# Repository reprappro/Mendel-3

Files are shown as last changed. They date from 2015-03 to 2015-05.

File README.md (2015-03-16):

The RepRapPro Mendel 3 3D Printer design files repository
.
Licensed under the GPL 3, see http://www.gnu.org/copyleft/gpl.html

For more information see 

   https://reprappro.com/shop/reprap-kits/mendel-3-full-kit/

STLs of the printed parts may be found in the STL directory. A full bill of materials - itemising part numbers, descriptions and required quantities - may be found in BOM.xlsx.

Hardware components that are shared with our other printers may be found in our "Library" repository

License GPL

No guarantee is made that the files contained in this project will be free
from design faults. The user accepts the risk that some issues may arise
from printing and assembling the files contained within this project. Users
are however encouraged to publish errors/improvements back to the originator.

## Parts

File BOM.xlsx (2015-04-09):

PART NUMBER | Revision | DESCRIPTION | Category | QTY.
394 | 00-000 | DUET | ELECTRONICS | 1
545 | 00-001 | PROXIMITY SENSOR PCB | ELECTRONICS | 1
597 | 01-000 | REGULATOR PCB | ELECTRONICS | 1
111 | 00-001 | M3X8 CAP HEAD | FASTENERS | 11
112 | 00-001 | M3X25MM CAP SCREW | FASTENERS | 8
204 | 00-000 | M3 NYLOC FULL NUT | FASTENERS | 17
212 | 00-001 | M3 PLAIN WASHER | FASTENERS | 20
230 | 00-000 | M5X215MM THREADED ROD | FASTENERS | 2
241 | 00-000 | M3X20MM CAP SCREW | FASTENERS | 10
242 | 00-001 | M3X16MM CAP SCREW | FASTENERS | 7
257 | 00-000 | M3X12 CAP SCREW | FASTENERS | 16
258 | 00-000 | M3 NUT | FASTENERS | 25
465 | 00-000 | M3X50 CAP HEAD | FASTENERS | 3
520 | 00-001 | M3X35 CAP SCREW | FASTENERS | 4
543 | 00-000 | M3X30 CAP SCREW | FASTENERS | 3
581 | 00-000 | VBFS-M3-5-16 | FASTENERS | 4
689 | 00-000 | M8 NUT | FASTENERS | 78
699 | 00-000 | M8 LOCK WASHER | FASTENERS | 78
712 | 00-000 | M5 FULL NUT | FASTENERS | 2
818 | 00-000 | M3X18MM MALE/FEMALE STANDOFF VBMP-M3-5.0-18 | FASTENERS | 6
918 | 00-000 | #4 x 1/2" BUTTON HEAD SELF TAPPING SCREW | FASTENERS | 4
101 | 00-000 | CARDBOARD BOX MENDEL | HARDWARE | 1
125 | 00-000 | GLASS PRINTING PLATE | HARDWARE | 1
133 | 00-000 | CABLE TIES | HARDWARE | 1
185 | 00-000 | MICROSWITCH | HARDWARE | 1
195 | 00-000 | 5MM POLYTUBE | HARDWARE | 2
197 | 00-000 | 2.4MM BLACK HEATSHIRNK | HARDWARE | 1
199 | 00-000 | IGUS CLIP BEARING - 8MM | HARDWARE | 4
234 | 00-000 | SD CARD | HARDWARE | 1
276 | 00-000 | 15X7MM SPRING | HARDWARE | 2
279 | 00-000 | 623 BEARING | HARDWARE | 4
285 | 00-000 | PCB JUMPER | HARDWARE | 2
286 | 00-000 | KAPTON TAPE | HARDWARE | 1
287 | 00-000 | LM8UU LINEAR BEARING | HARDWARE | 6
310 | 00-000 | 608 BEARING | HARDWARE | 2
320 | 00-000 | MXL BELT - 2M | HARDWARE | 1
358 | 00-000 | 100M PLASTIC REEL OF 1.75MM PLA | HARDWARE | 1
408 | 00-000 | NEMA 17 | HARDWARE | 4
415 | 00-000 | USB A TO MICRO B | HARDWARE | 1
498 | 00-000 | HEAT SPREADER | HARDWARE | 1
504 | 00-000 | PLASTIC SET SQUARE | HARDWARE | 1
507 | 00-000 | POWERCORD UK | HARDWARE | 1
551 | 00-000 | BED CLIPS | HARDWARE | 4
576 | 00-000 | DUET ENCLOSURE BASE | HARDWARE | 1
577 | 00-000 | DUET ENCLOSURE LID | HARDWARE | 1
578 | 03-000 | DUET PERIMETER | HARDWARE | 1
583 | 00-000 | ALUMINIUM FOIL | HARDWARE | 1
591 | 00-000 | DC POWER CABLE 120MM | HARDWARE | 1
592 | 00-000 | AC POWER CABLE - 90MM | HARDWARE | 1
598 | 00-000 | IEC MAINS FUSED SWITCH SOCKET | HARDWARE | 1
599 | 00-000 | FUSE 5A 20MM | HARDWARE | 1
651 | 00-000 | M4X10mm BUTTON HEAD SCREW | HARDWARE | 4
668 | 00-000 | EARTH LOOP | HARDWARE | 1
677 | 00-000 | DC POWER LINK | HARDWARE | 1
698 | 00-000 | CRIMPTED 10K NTC BED | HARDWARE | 1
782 | 00-000 | 18 TOOTH MXL PULLEY | HARDWARE | 2
798 | 00-000 | ELECTRONICS DUET BOX | HARDWARE | 1
822 | 00-000 | OUTER PSU PLATE | HARDWARE | 1
823 | 01-000 | PSU SPACER | HARDWARE | 1
824 | 00-000 | PSU COVER SPACER | HARDWARE | 1
831 | 00-000 | SP-200 12V POWER SUPPLY | HARDWARE | 1
911 | 00-000 | M8x370mm THREADED ROD | HARDWARE | 6
913 | 01-000 | HEATBED INSULATOR | HARDWARE | 1
915 | 00-000 | Y SLED | HARDWARE | 1
929 | 00-000 | M8x330mm THREADED ROD | HARDWARE | 4
930 | 00-000 | M8x465mm THREADED ROD | HARDWARE | 2
931 | 00-000 | M8x445mm THREADED ROD | HARDWARE | 2
932 | 00-000 | 395x8MM SMOOTH ROD | HARDWARE | 2
933 | 00-000 | 342x8MM SMOOTH ROD | HARDWARE | 2
934 | 00-000 | 426X8MM SMOOTH ROD | HARDWARE | 2
942 | 00-000 | INNER PSU PLATE (MENDEL) | HARDWARE | 1
946 | 00-000 | 3x13mm NYLON SPACER | HARDWARE | 1
950 | 00-000 | MEASURING JIG | HARDWARE | 1
951 | 00-000 | CE STICKER MENDEL | HARDWARE | 1
955 | 00-000 | HEATBED PCB | HARDWARE | 1
325 | 00-000 | Y MOTOR MOUNT | LASERCUT | 2
826 | 00-000 | INNER PSU SPACER | LASERCUT | 1
923 | 00-000 | Y BELT CLAMP | LASERCUT | 2
264 | 00-000 | Y BAR CLAMP | PRINTED PARTS | 7
295 | 01-000 | Z MOTOR MOUNT | PRINTED PARTS | 2
322 | 00-000 | BELT GUIDE | PRINTED PARTS | 4
339 | 00-000 | X IDLER COVER | PRINTED PARTS | 1
609 | 00-002 | Z COUPLING | PRINTED PARTS | 4
820 | 00-000 | PSU COVER | PRINTED PARTS | 1
910 | 00-000 | FRAME VERTEX WITH FOOT | PRINTED PARTS | 2
1010 | 00-000 | FRAME VERTEX WITH FOOT(MIRRORED) | PRINTED PARTS | 2
912 | 00-000 | FRAME VERTEX WITHOUT FOOT | PRINTED PARTS | 2
914 | 00-000 | Y BEARING HOLDER | PRINTED PARTS | 3
916 | 00-001 | NOZZLE MOUNT | PRINTED PARTS | 1
917 | 00-002 | FAN MOUNT | PRINTED PARTS | 1
935 | 00-000 | BAR CLAMP WITH ENDSTOP MOUNT | PRINTED PARTS | 1
939 | 00-000 | ELECTRONICS BAR CLAMP | PRINTED PARTS | 2
940 | 00-000 | ELECTRONICS BAR CLAMP 2 | PRINTED PARTS | 1
945 | 00-000 | X MOTOR SPACER | PRINTED PARTS | 1
947 | 00-000 | X CARRIAGE | PRINTED PARTS | 1
948 | 00-000 | X END IDLER | PRINTED PARTS | 1
949 | 00-000 | X END MOTOR | PRINTED PARTS | 1
579 | 01-002 | MOTOR SHIELD | SHEET METAL | 4

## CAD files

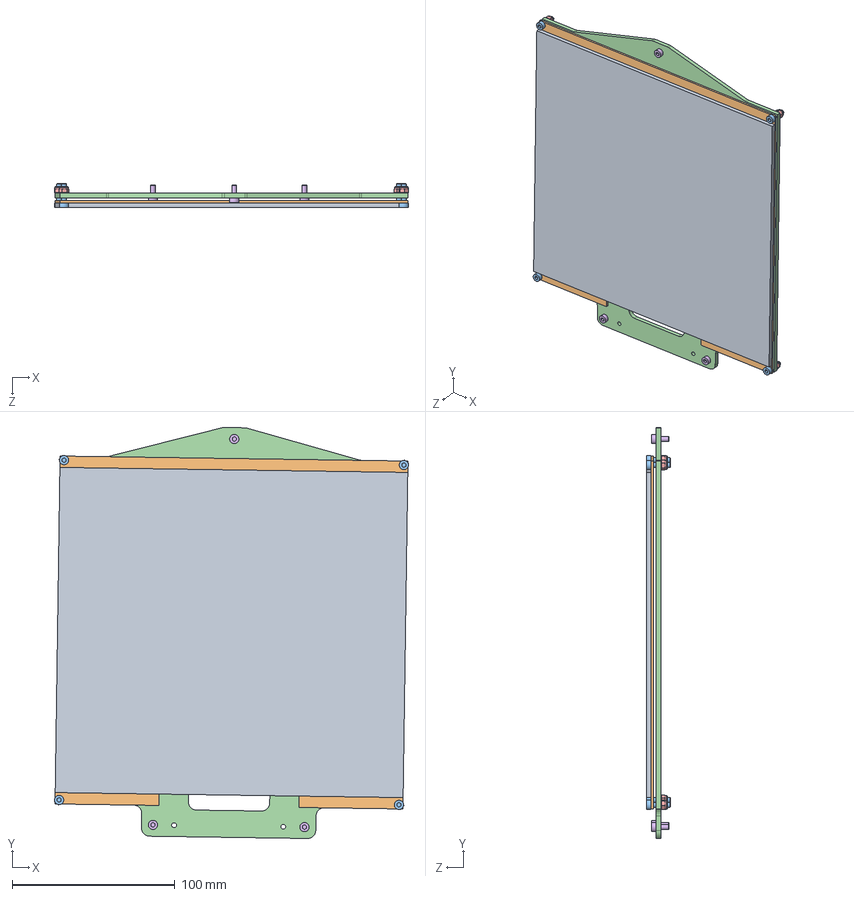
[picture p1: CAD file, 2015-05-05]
980.SLDASM
217.9 x 252.8 x 15.0 mm

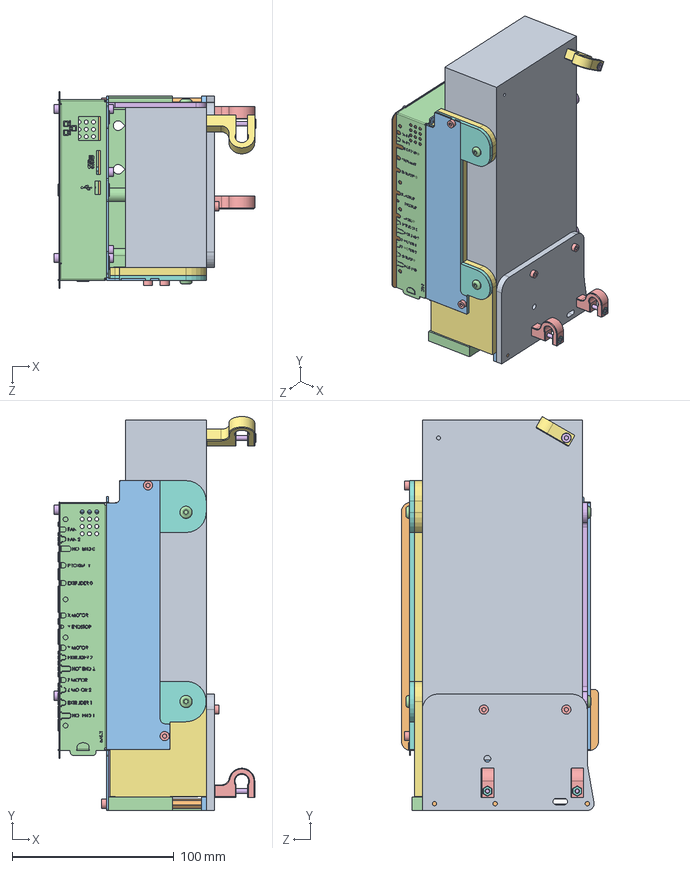
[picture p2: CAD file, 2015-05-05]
938.SLDASM
124.8 x 243.6 x 122.0 mm

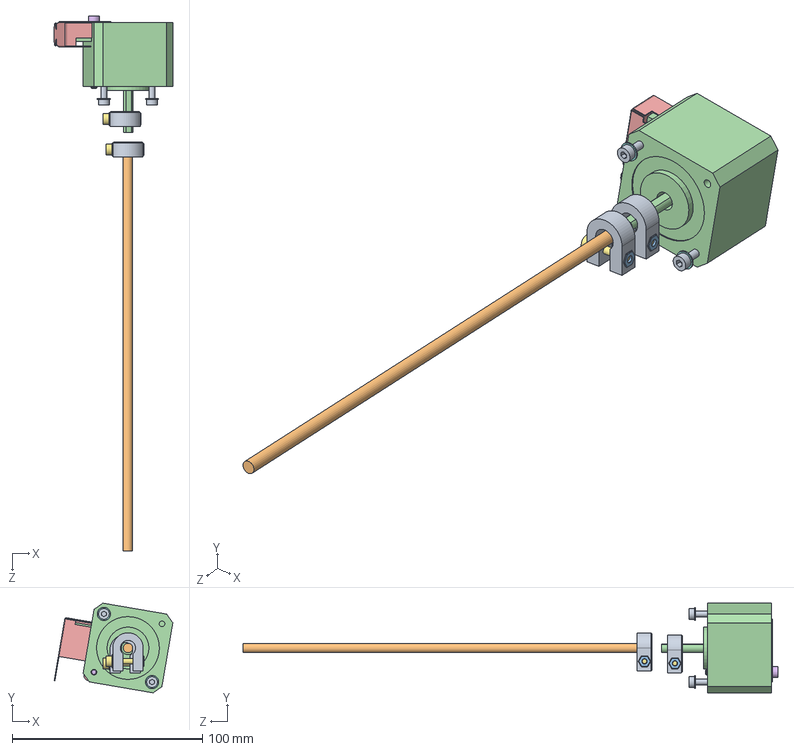
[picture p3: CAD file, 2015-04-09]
943.SLDASM
62.4 x 47.1 x 281.1 mm

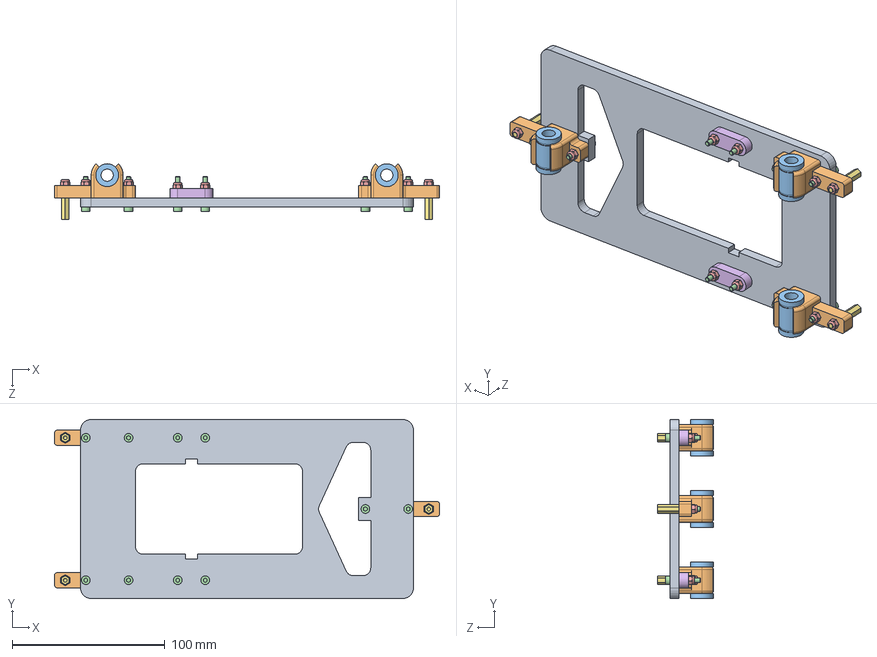
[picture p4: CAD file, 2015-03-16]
1090.SLDASM
252.0 x 117.2 x 36.3 mm

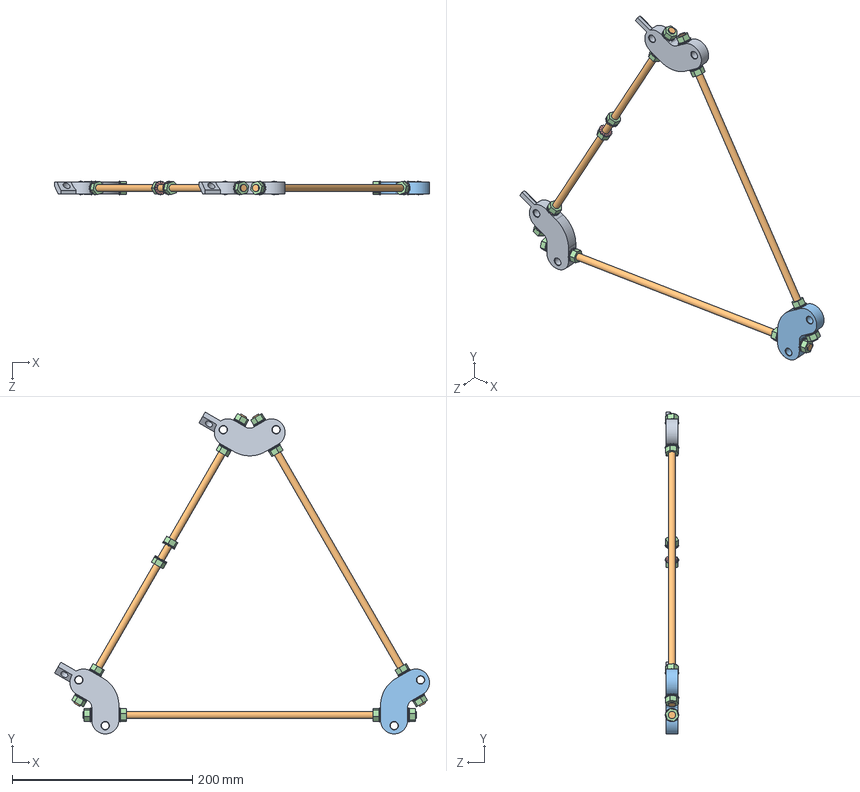
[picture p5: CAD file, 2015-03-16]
1088.SLDASM
415.6 x 356.7 x 15.0 mm

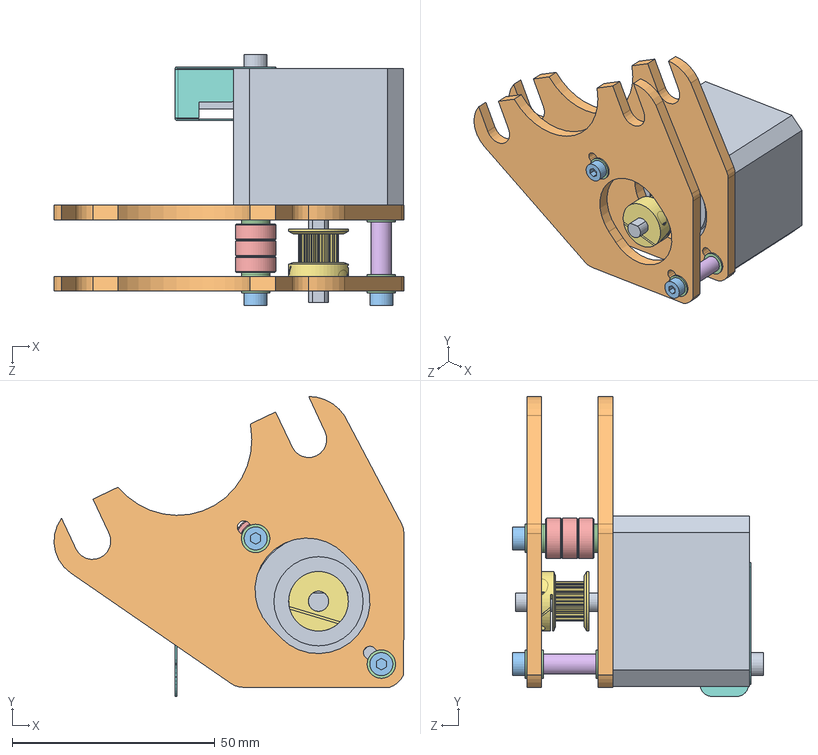
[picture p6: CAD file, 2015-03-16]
1091.SLDASM
86.3 x 74.0 x 61.8 mm

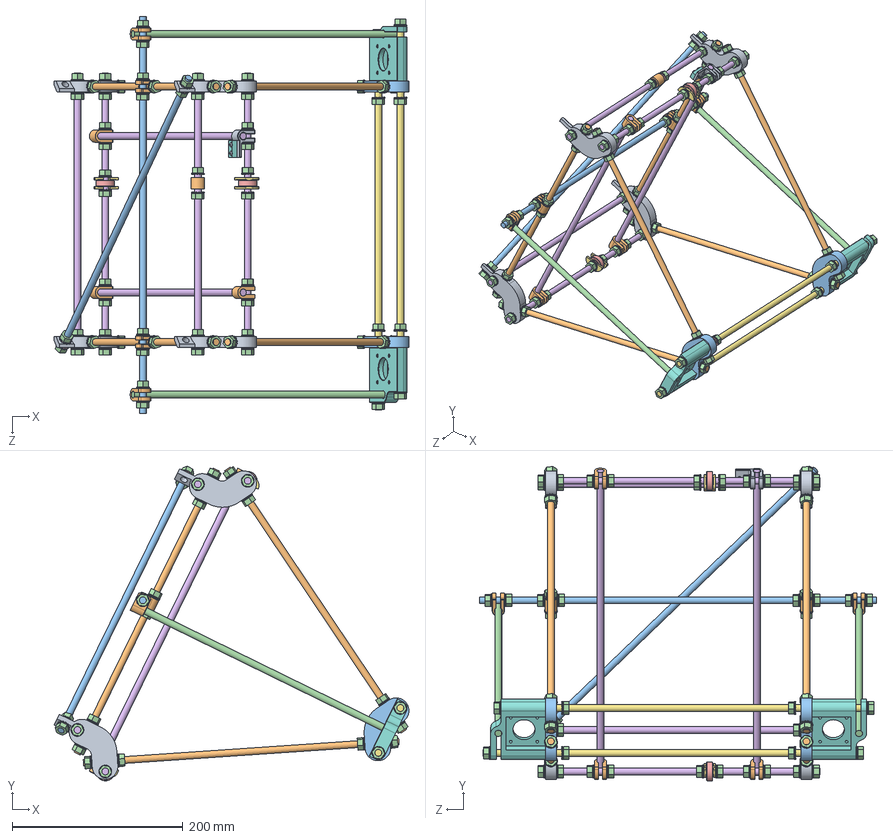
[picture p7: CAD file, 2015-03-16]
1087.SLDASM
415.4 x 368.2 x 465.0 mm

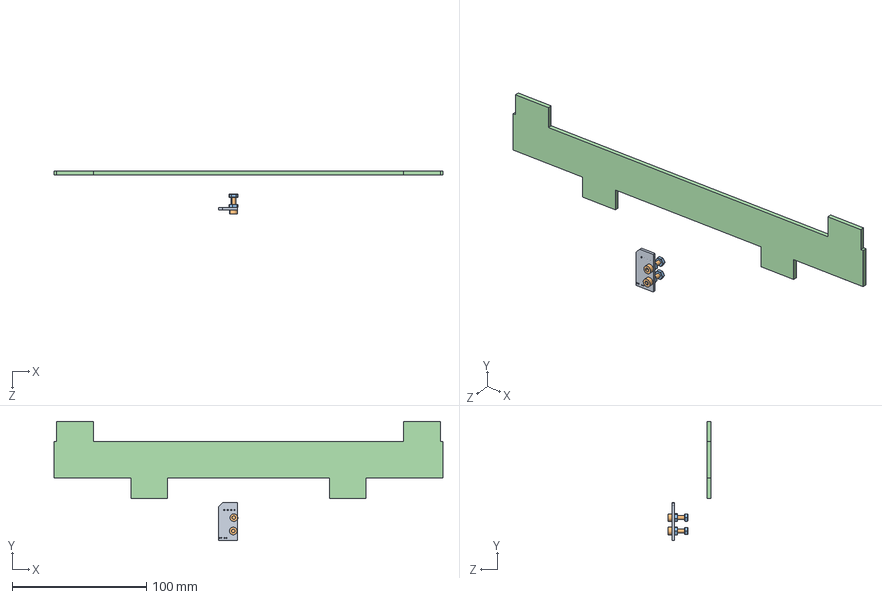
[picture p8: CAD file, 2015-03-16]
1084.SLDASM
290.0 x 88.8 x 32.4 mm

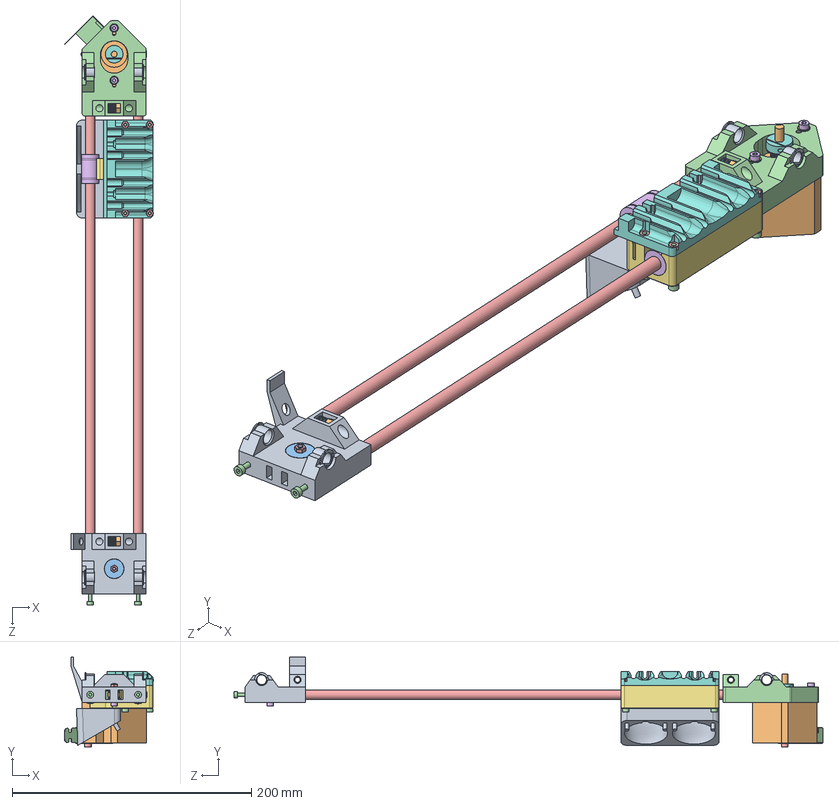
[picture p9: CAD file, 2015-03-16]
1089.SLDASM
74.6 x 75.2 x 492.5 mm

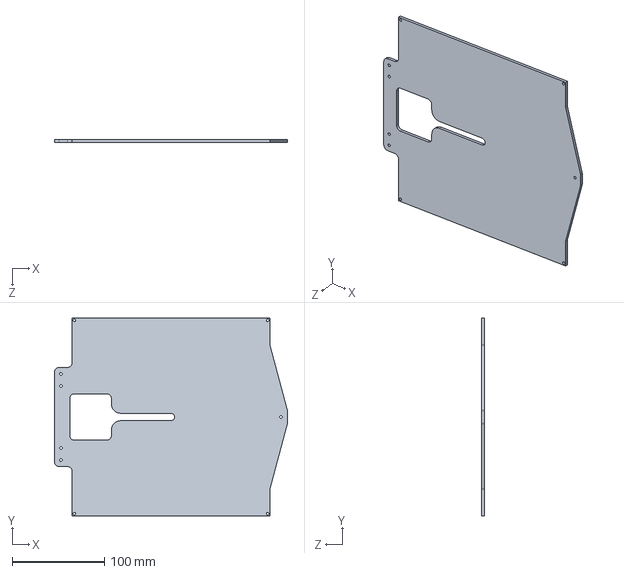
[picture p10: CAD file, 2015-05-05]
913.SLDPRT
252.0 x 214.0 x 3.00 mm

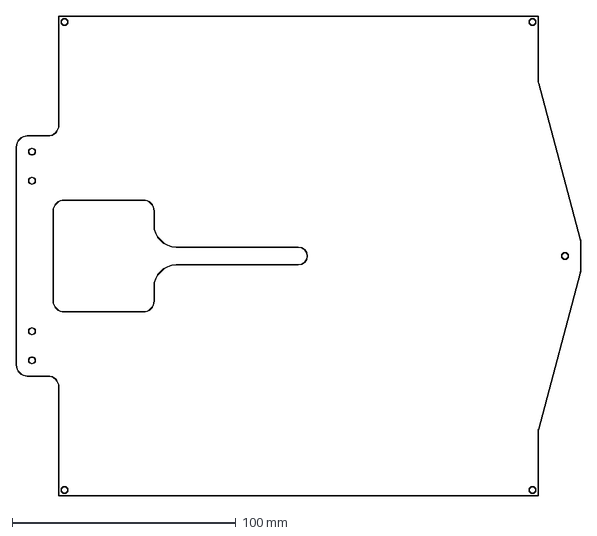
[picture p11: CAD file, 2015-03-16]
DXF/913.1.DXF
252.0 x 214.0 mm

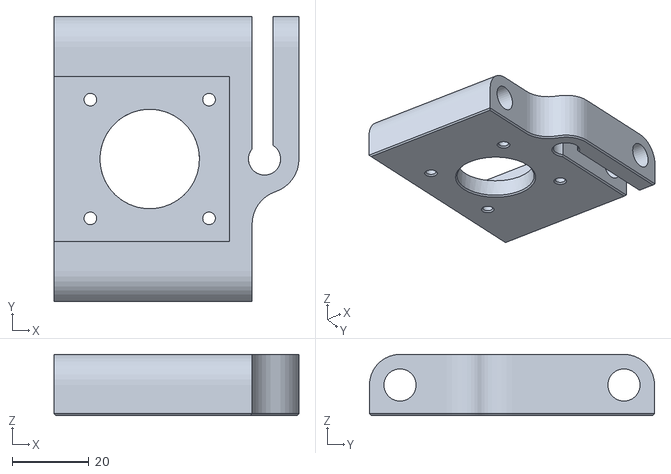
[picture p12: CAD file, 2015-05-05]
STLs/295.1.STL
64.0 x 74.5 x 16.0

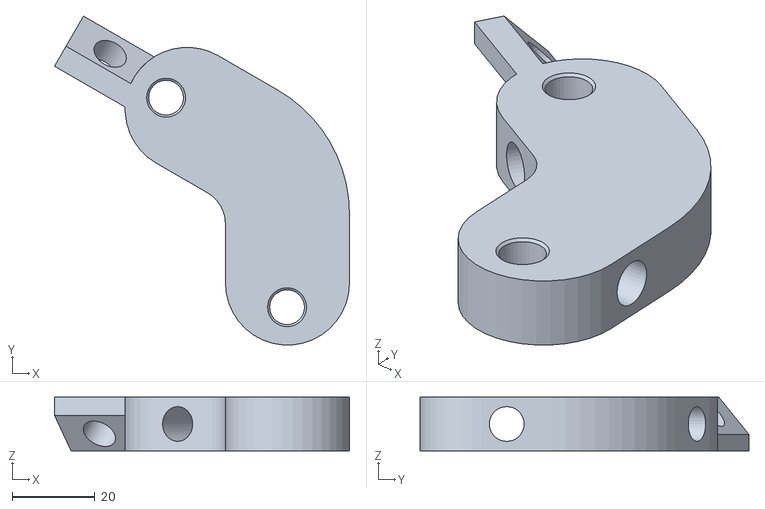
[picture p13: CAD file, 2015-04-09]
STLs/1010.STL
71.3 x 79.5 x 13.0

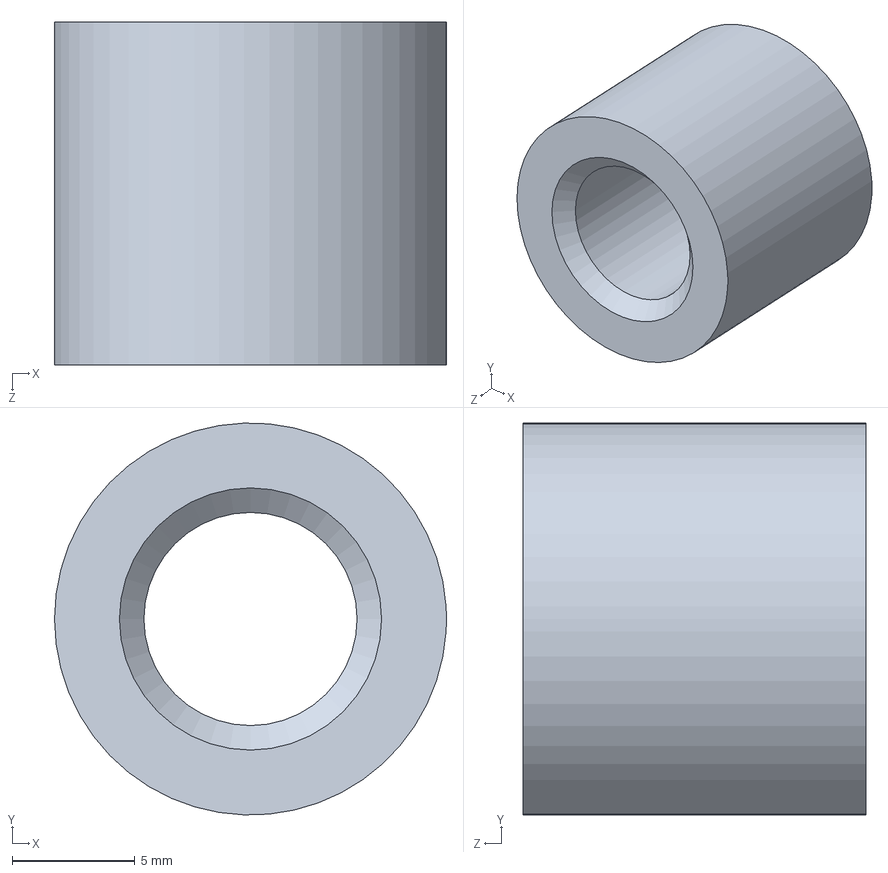
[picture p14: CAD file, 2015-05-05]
945.SLDPRT
16.0 x 16.0 x 14.0 mm

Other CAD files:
914.SLDPRT
934.SLDPRT
339.SLDPRT
933.SLDPRT
1013.SLDPRT
264.SLDPRT
295.SLDPRT
322.SLDPRT
325.SLDPRT
498.SLDPRT
910.SLDPRT
911.SLDPRT
912.SLDPRT
915.SLDPRT
916.SLDPRT
917.SLDPRT
923.SLDPRT
929.SLDPRT
930.SLDPRT
931.SLDPRT
932.SLDPRT
935.SLDPRT
939.SLDPRT
940.SLDPRT
947.SLDPRT
948.SLDPRT
949.SLDPRT
950.SLDPRT
951.SLDPRT
DXF/325.DXF
DXF/913.DXF
DXF/915.DXF
DXF/923.DXF
DXF/950.dxf
STLs/264.STL
STLs/322.STL
STLs/339.STL
STLs/910.STL
STLs/912.STL
STLs/914.STL
STLs/916.STL
STLs/917.STL
STLs/935.STL
STLs/939.STL
STLs/940.STL
STLs/945.STL
STLs/947.STL
STLs/948.STL
STLs/949.STL

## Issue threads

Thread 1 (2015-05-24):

Regarding 916

JamesT42, 2015-05-24:
There is one extra chamfer on the front, just on one hole

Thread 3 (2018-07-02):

Reprappro mendel 3 assembly instructions

Silviu-Muntean, 2018-07-02:
Hello,

i'm trying to build the RepRapPro Mendel 3 3d printer,the one that has all printed parts in green,laser-cut wood parts and Duet 06 with Duex extension board.

Is there a tutorial still avalable on how to assembly this printer?
I tried to go to reprap.org and search there,but all tutorials there on Mendel Tricolor are not for my Mendel 3 printer. Also here on git, the link in the description is not working.
Also i can't find .stl files for the gear mechanism that pushes the filament.

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

Any information is appreciated. And sorry for my English.
Regards,
Silviu.

Silviu-Muntean, 2018-07-02:
Thanks Sally. :) The link of all the parts necessary and documentations on how to build use and maintain are here : https://reprapltd.com/reprappro/documentation/mendel-3/index.html#General_notes . Also here https://reprapltd.com/reprappro/documentation/huxley-duo/troubleshooting/index.html in the red warning box where it said that every info is out of date you have links to more stuff. Issue solved.

Closed 2018-07-02.

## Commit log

2015-03-16 First release
    [1013.SLDPRT, 1084.SLDASM, 1087.SLDASM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]
2015-03-18 Moving electronics assembly to Library
    [937.SLDASM, 938.SLDASM]
2015-04-09 Adding mirrored stl
    [910-mirrored.STL, 938.SLDASM, 943.SLDASM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]
2015-04-09 Updating BOM for mirrored STL
    [1010.STL, BOM.xlsx]
2015-05-05 Reorientating STLs
    [264.STL, 295.1.STL, 913.SLDPRT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]
